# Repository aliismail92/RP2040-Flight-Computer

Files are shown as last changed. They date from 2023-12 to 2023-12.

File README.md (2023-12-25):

# RP2040-Flight-Computer
This is a custom drone flight computer based on RP2040. The KiCad files are available in addition to the production files to be produced by JLC PCB.

The Flight computer has the following sensors:
  - MPU 6050 Inertia sensor
  - HMC5883L digital compass sensor
  - BMP280 pressure sensor

Other specified connectors that can be added:
  - SD-card connector at the bottom of the board
  - Two uart connectors for the Radio controller (tagged IBUS) and another for GPS (tagged GPS)
  - Broken GPIOs for NRF24L01 with proper pin locations

Additionally, the two I2C ports connected to the MPU6050 and BMP280 have the pins exposed for debugging purposes.

The board was produced and assembled by JLCPCB and working.

RP2040-Brain-v2 0

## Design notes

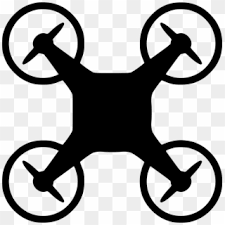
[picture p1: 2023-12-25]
images.png

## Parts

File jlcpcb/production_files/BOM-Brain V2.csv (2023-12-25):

Comment | Designator | Footprint | LCSC
1K | R2,R4 | R_0402_1005Metric | C11702
USB_B_Micro | J1 | USB_Micro-B_Molex-105017-0001 | C136000
10nF | C18 | C_0402_1005Metric | C15195
100nF | C10,C11,C12,C13,C14,C15,C16,C20,C21,C22,C23,C26,C28,C29,C3,C4,C6 | C_0402_1005Metric | C1525
30pF | C1,C2 | C_0402_1005Metric | C1562
2.2nF | C24 | C_0603_1608Metric | C1604
220nf | C30 | C_0402_1005Metric | C16772
4.7uF | C33,C7 | C_0603_1608Metric | C19666
10u | C25 | C_0603_1608Metric | C19702
RP2040 | U6 | QFN-56-1EP_7x7mm_P0.4mm_EP4x4mm_ThermalVias | C2040
1k | R18,R5 | R_0603_1608Metric | C21190
LED | D2,D3 | LED_0603_1608Metric | C2290
MPU-6050 | U4 | InvenSense_QFN-24_4x4mm_P0.5mm_NoMask | C24112
27 | R10,R9 | R_0603_1608Metric | C25190
10K | R1,R11,R12,R13,R14,R15,R16,R17,R19,R3,R6,R7 | R_0402_1005Metric | C25744
2.2K | R8 | R_0402_1005Metric | C25879
D_Schottky | D1 | D_SMA | C2909963
1u | C17,C19,C27 | C_0402_1005Metric_Pad0.74x0.62mm_HandSolder | C52923
22uF | C31,C5,C8,C9 | C_0603_1608Metric | C59461
AMS1117-3.3 | U2 | SOT-223-3_TabPin2 | C6186
BMP280 | U5 | Bosch_LGA-8_2x2.5mm_P0.65mm_ClockwisePinNumbering | C83291
Crystal_GND24 | Y1 | Crystal_SMD_3225-4Pin_3.2x2.5mm | C9002
W25Q128JVS | U1 | SOIC-8_5.23x5.23mm_P1.27mm | C97521

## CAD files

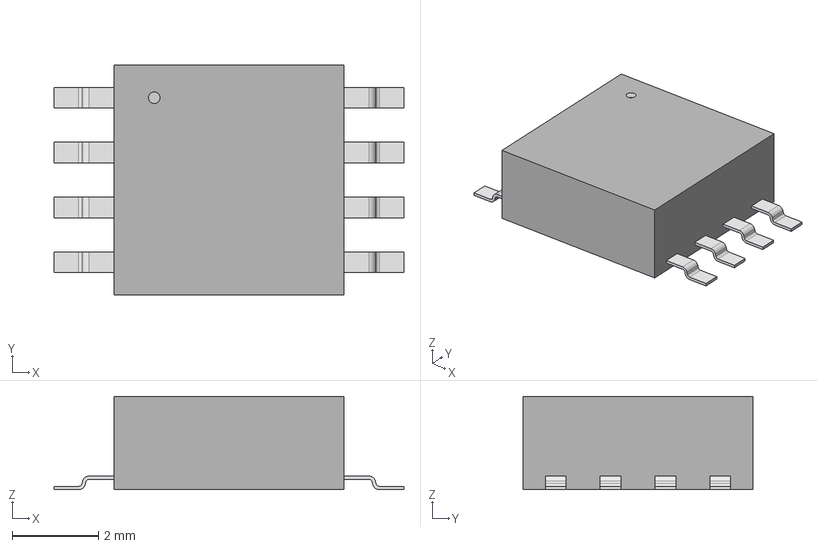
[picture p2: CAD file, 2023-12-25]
00-External Components/W25Q128_3D/SOIC_128JVSIM_WIN.step
8.10 x 5.33 x 2.16 mm

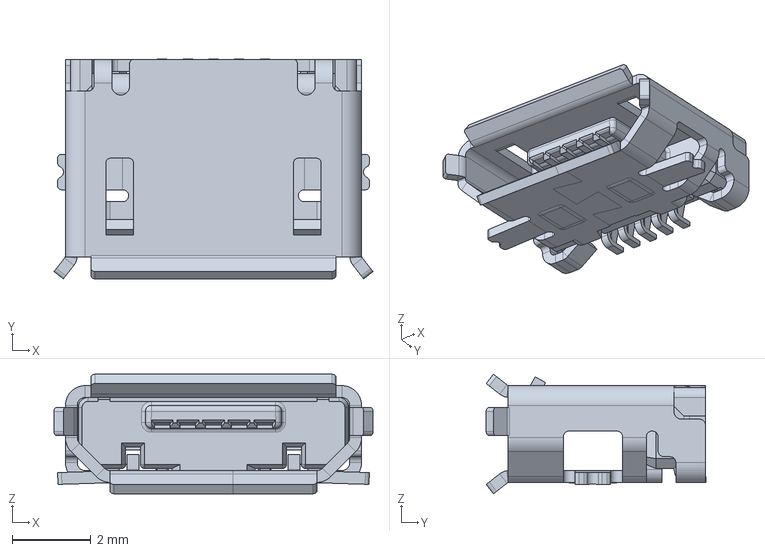
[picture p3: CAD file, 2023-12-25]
00-External Components/10104110-0001LF--3DModel-STEP-533217.STEP
8.08 x 5.56 x 3.03 mm

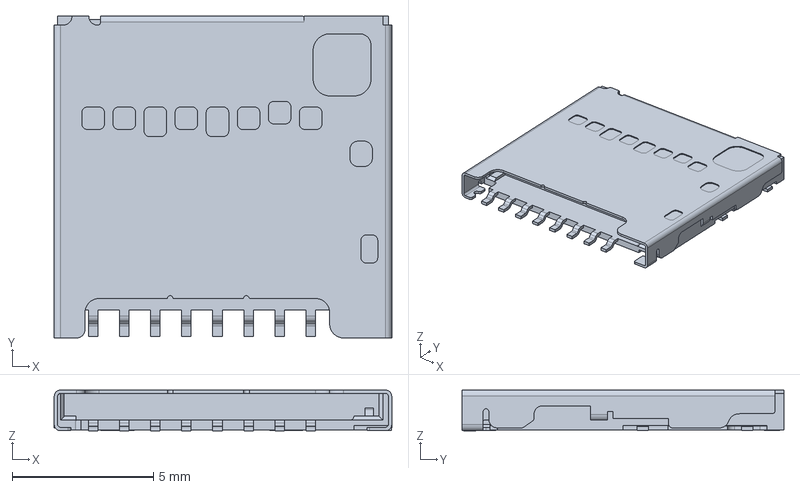
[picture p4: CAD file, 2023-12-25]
00-External Components/Molex 104031_SD_3D/1040310811.stp
11.9 x 11.4 x 1.45 mm

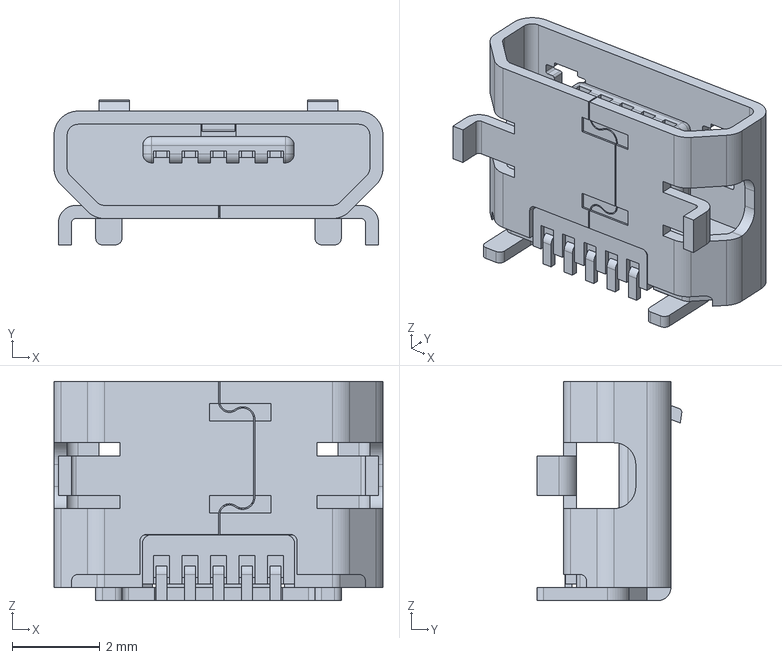
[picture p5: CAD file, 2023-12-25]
00-External Components/Molex 1050171_3D/1050171001.stp
7.50 x 3.30 x 5.00 mm

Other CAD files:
EdgeCut.dwg

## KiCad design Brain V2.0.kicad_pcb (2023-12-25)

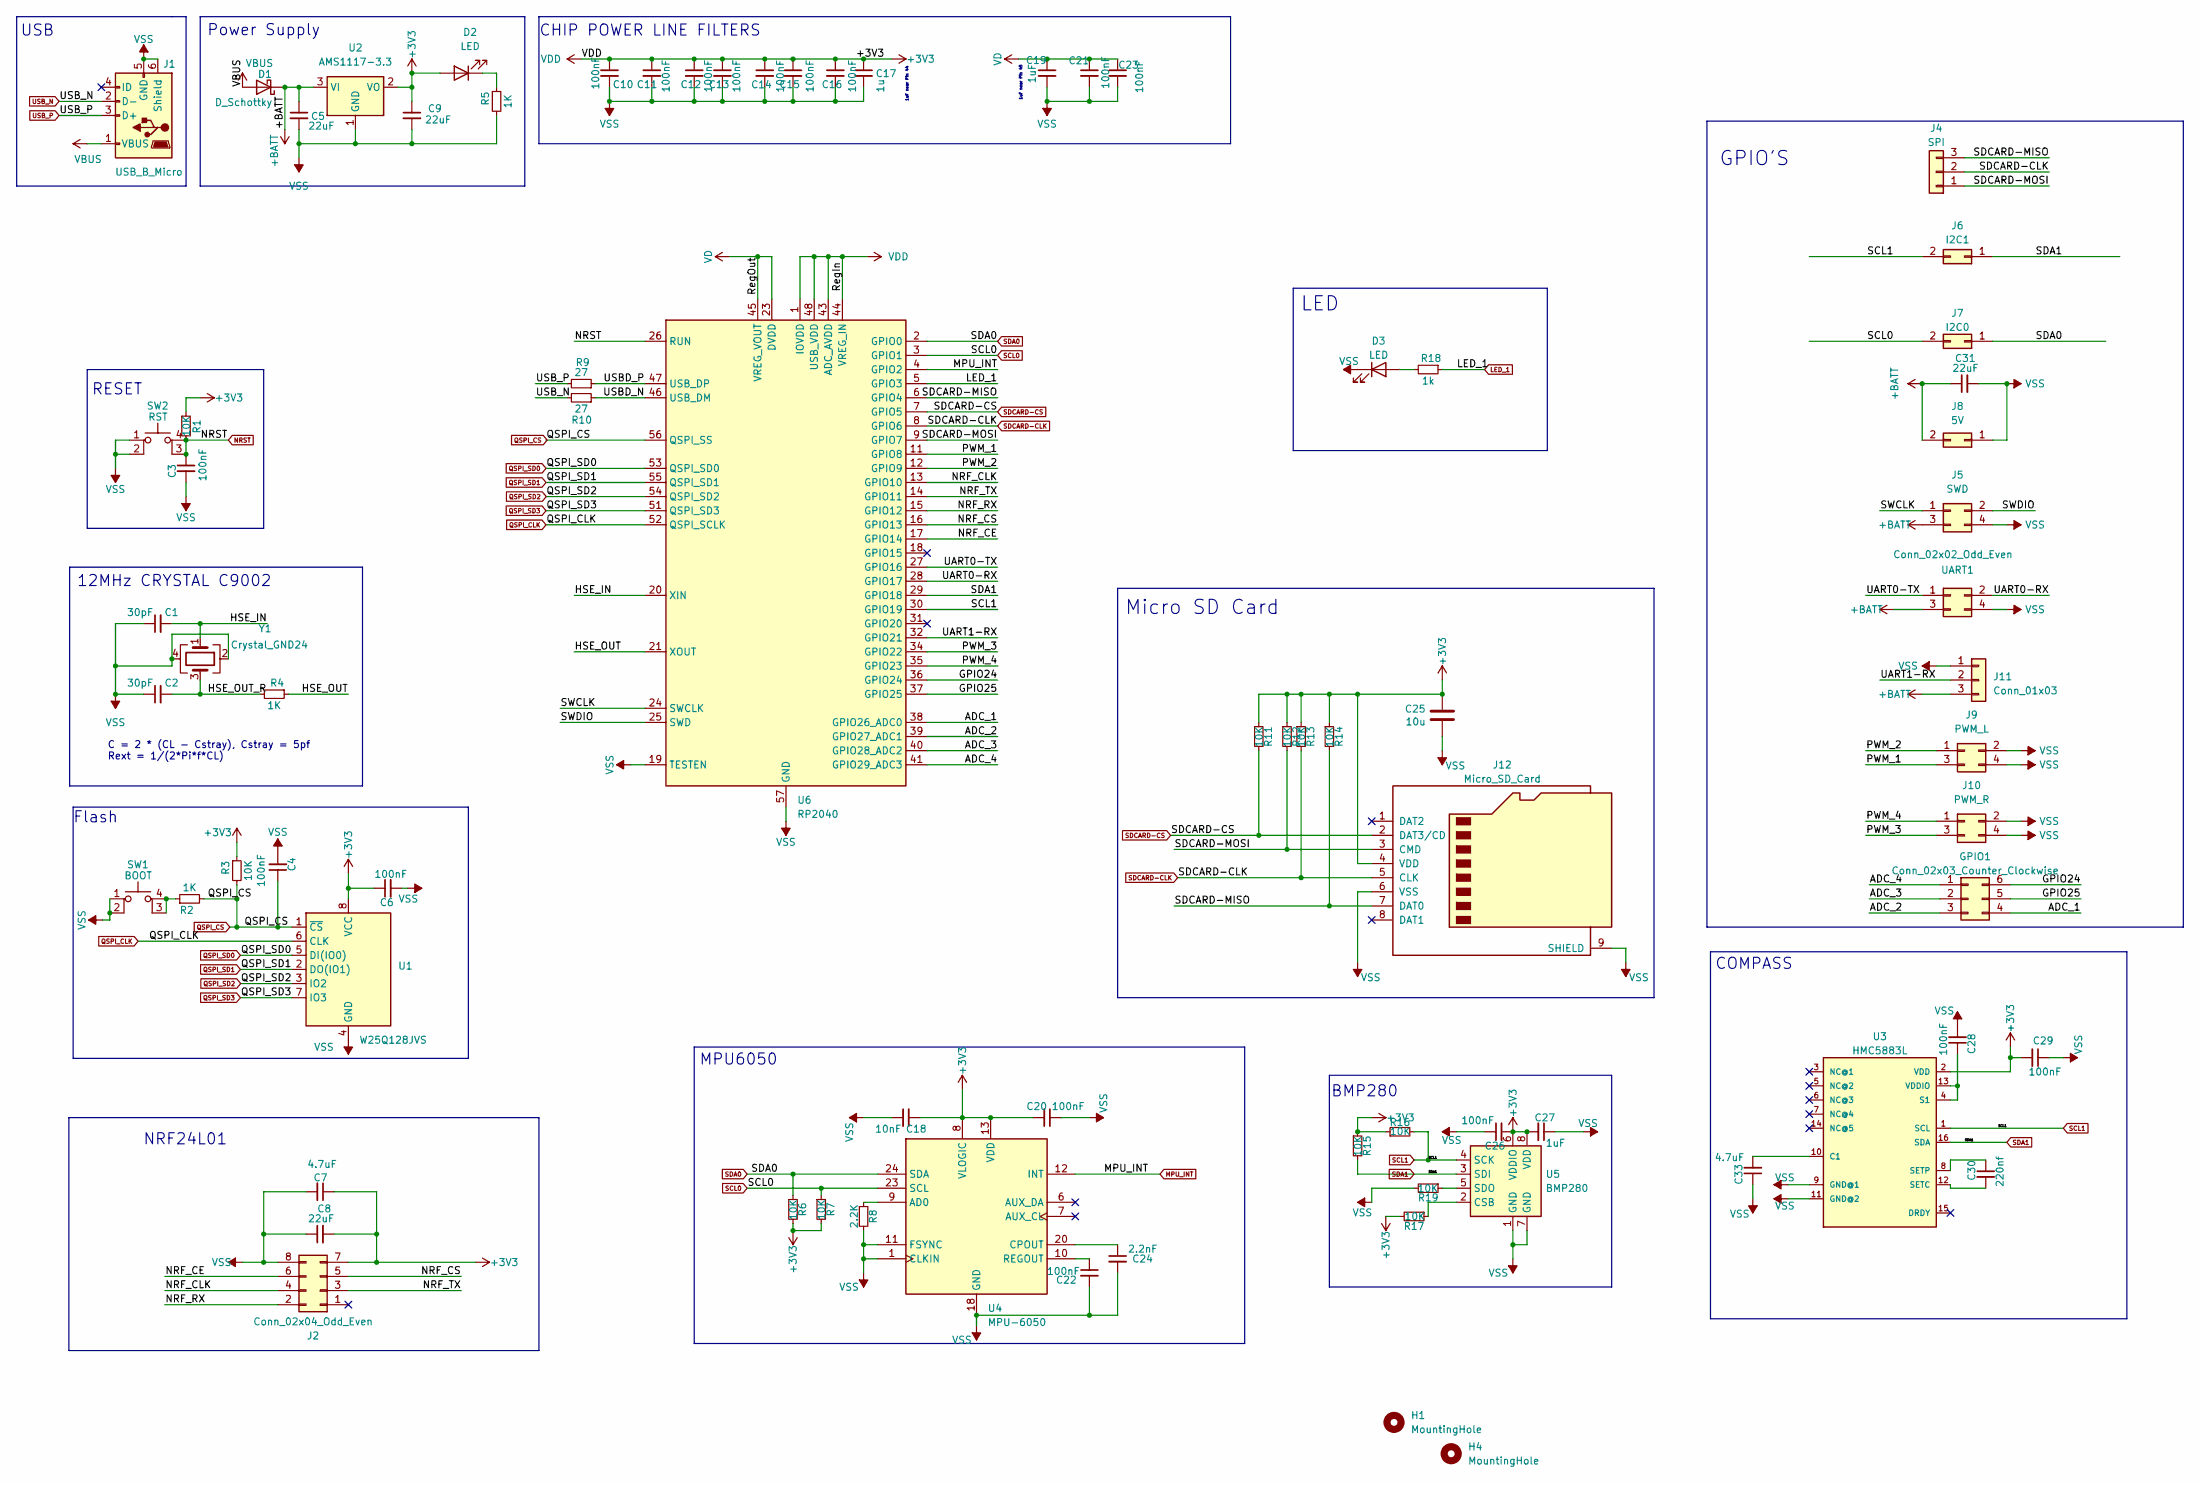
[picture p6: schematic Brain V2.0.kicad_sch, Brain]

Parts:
C1, C2: 30pF; C_0402_1005Metric
C3, C4, C6, C10, C11, C12, C13, C14, C15, C16, C20, C21, C22, C23, C26, C28, C29: 100nF; C_0402_1005Metric
C5, C8, C9, C31: 22uF; C_0603_1608Metric
C7, C33: 4.7uF; C_0603_1608Metric
C17: 1u; C_0402_1005Metric_Pad0.74x0.62mm_HandSolder
C18: 10nF; C_0402_1005Metric
C19: 1uF; C_0402_1005Metric_Pad0.74x0.62mm_HandSolder
C24: 2.2nF; C_0603_1608Metric
C25: 10u; C_0603_1608Metric
C27: 1uF; C_0402_1005Metric
C30: 220nf; C_0402_1005Metric
D1: D_Schottky; D_SMA
D2, D3: LED; LED_0603_1608Metric
GPIO1: Conn_02x03_Counter_Clockwise; PinHeader_2x03_P2.54mm_Vertical
H1, H4: MountingHole; MountingHole_4.3mm_M4
J1: USB_B_Micro; USB_Micro-B_Molex-105017-0001
J2: Conn_02x04_Odd_Even; PinHeader_2x04_P2.54mm_Vertical
J4: SPI; PinHeader_1x03_P2.54mm_Vertical
J5: SWD; PinHeader_2x02_P2.54mm_Vertical
J6: I2C1; PinHeader_2x01_P2.54mm_Vertical
J7: I2C0; PinHeader_2x01_P2.54mm_Vertical
J8: 5V; PinHeader_2x01_P2.54mm_Vertical
J9: PWM_L; PinHeader_2x02_P2.54mm_Vertical
J10: PWM_R; PinHeader_2x02_P2.54mm_Vertical
J11: Conn_01x03; JST_XH_B3B-XH-AM_1x03_P2.50mm_Vertical
J12: Micro_SD_Card; microSD_HC_Molex_104031-0811
R1, R3, R6, R7, R11, R12, R13, R14, R15, R16, R17, R19: 10K; R_0402_1005Metric
R2, R4: 1K; R_0402_1005Metric
R5: 1K; R_0603_1608Metric
R8: 2.2K; R_0402_1005Metric
R9, R10: 27; R_0603_1608Metric
R18: 1k; R_0603_1608Metric
SW1: BOOT; Button-01
SW2: RST; Button-01
U1: W25Q128JVS; SOIC-8_5.23x5.23mm_P1.27mm
U2: AMS1117-3.3; SOT-223-3_TabPin2
U3: HMC5883L; LPCC-16
U4: MPU-6050; InvenSense_QFN-24_4x4mm_P0.5mm_NoMask
U5: BMP280; Bosch_LGA-8_2x2.5mm_P0.65mm_ClockwisePinNumbering
U6: RP2040; QFN-56-1EP_7x7mm_P0.4mm_EP4x4mm_ThermalVias
UART1: Conn_02x02_Odd_Even; JST_XH_B4B-XH-A_1x04_P2.50mm_Vertical
Y1: Crystal_GND24; Crystal_SMD_3225-4Pin_3.2x2.5mm

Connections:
+3V3: C6.1, C7.1, C8.2, C9.1, C10.1, C11.1, C12.1, C13.1, C14.1, C15.1, C16.1, C17.1, C18.2, C20.2, C25.1, C26.2, C27.2, C29.2, D2.2 (A), J2.7, J12.4 (VDD), R1.1, R3.1, R6.2, R7.2, R11.1, R12.1, R13.1, R14.1, R15.1, R16.1, R17.2, U1.8 (VCC), U2.2 (VO), U3.2 (VDD), U4.8 (VLOGIC), U4.13 (VDD), U5.6 (VDDIO), U5.8 (VDD), U6.1 (IOVDD), U6.10 (IOVDD), U6.22 (IOVDD), U6.33 (IOVDD), U6.42 (IOVDD), U6.43 (ADC_AVDD), U6.44 (VREG_IN), U6.48 (USB_VDD), U6.49 (IOVDD)
+BATT: C5.1, C31.1, D1.1 (K), J5.3, J8.2, J11.3, U2.3 (VI), UART1.3
/ADC_1: GPIO1.4, U6.38 (GPIO26_ADC0)
/ADC_2: GPIO1.3, U6.39 (GPIO27_ADC1)
/ADC_3: GPIO1.2, U6.40 (GPIO28_ADC2)
/ADC_4: GPIO1.1, U6.41 (GPIO29_ADC3)
/GPIO24: GPIO1.6, U6.36 (GPIO24)
/GPIO25: GPIO1.5, U6.37 (GPIO25)
/HSE_IN: C1.2, U6.20 (XIN), Y1.1
/HSE_OUT: R4.1, U6.21 (XOUT)
/HSE_OUT_R: C2.2, R4.2, Y1.3
/NRF_CE: J2.6, U6.17 (GPIO14)
/NRF_CLK: J2.4, U6.13 (GPIO10)
/NRF_CS: J2.5, U6.16 (GPIO13)
/NRF_RX: J2.2, U6.15 (GPIO12)
/NRF_TX: J2.3, U6.14 (GPIO11)
/PWM_1: J9.3, U6.11 (GPIO8)
/PWM_2: J9.1, U6.12 (GPIO9)
/PWM_3: J10.3, U6.34 (GPIO22)
/PWM_4: J10.1, U6.35 (GPIO23)
/SDCARD-MISO: J4.3, J12.7 (DAT0), R14.2, U6.6 (GPIO4)
/SDCARD-MOSI: J4.1, J12.3 (CMD), R12.2, U6.9 (GPIO7)
/SWCLK: J5.1, U6.24 (SWCLK)
/SWDIO: J5.2, U6.25 (SWD)
/UART0-RX: U6.28 (GPIO17), UART1.2
/UART0-TX: U6.27 (GPIO16), UART1.1
/UART1-RX: J11.2, U6.32 (GPIO21)
/USBD_N: R10.1, U6.46 (USB_DM)
/USBD_P: R9.1, U6.47 (USB_DP)
LED_1: R18.1, U6.5 (GPIO3)
MPU_INT: U4.12 (INT), U6.4 (GPIO2)
NRST: C3.1, R1.2, SW2.3 (K), SW2.4 (A), U6.26 (RUN)
unnamed: D2.1 (K), R5.1
unnamed: D3.2 (A), R18.2
unnamed: R2.1, SW1.3 (K), SW1.4 (A)
unnamed: C33.2, U3.10 (C1)
unnamed: C28.1, U3.4 (S1), U3.13 (VDDIO)
unnamed: C30.2, U3.12 (SETC)
unnamed: C30.1, U3.8 (SETP)
unnamed: R8.1, U4.9 (AD0)
unnamed: C24.1, U4.20 (CPOUT)
unnamed: C22.1, U4.10 (REGOUT)
unnamed: R17.1, U5.2 (CSB)
unnamed: R19.1, U5.5 (SDO)
QSPI_CLK: U1.6 (CLK), U6.52 (QSPI_SCLK)
QSPI_CS: C4.1, R2.2, R3.2, U1.1 (~CS), U6.56 (QSPI_SS)
QSPI_SD0: U1.5 (DI(IO0)), U6.53 (QSPI_SD0)
QSPI_SD1: U1.2 (DO(IO1)), U6.55 (QSPI_SD1)
QSPI_SD2: U1.3 (IO2), U6.54 (QSPI_SD2)
QSPI_SD3: U1.7 (IO3), U6.51 (QSPI_SD3)
SCL0: J7.2, R7.1, U4.23 (SCL), U6.3 (GPIO1)
SCL1: J6.2, R16.2, U3.1 (SCL), U5.4 (SCK), U6.30 (GPIO19)
SDA0: J7.1, R6.1, U4.24 (SDA), U6.2 (GPIO0)
SDA1: J6.1, R15.2, U3.16 (SDA), U5.3 (SDI), U6.29 (GPIO18)
SDCARD-CLK: J4.2, J12.5 (CLK), R13.2, U6.8 (GPIO6)
SDCARD-CS: J12.2 (DAT3/CD), R11.2, U6.7 (GPIO5)
USB_N: J1.2 (D-), R10.2
USB_P: J1.3 (D+), R9.2
VBUS: D1.2 (A), J1.1 (VBUS)
VD: C19.1, C21.1, C23.1, U6.23 (DVDD), U6.45 (VREG_VOUT), U6.50 (DVDD)
VSS: C1.1, C2.1, C3.2, C4.2, C5.2, C6.2, C7.2, C8.1, C9.2, C10.2, C11.2, C12.2, C13.2, C14.2, C15.2, C16.2, C17.2, C18.1, C19.2, C20.1, C21.2, C22.2, C23.2, C24.2, C25.2, C26.1, C27.1, C28.2, C29.1, C31.2, C33.1, D3.1 (K), J1.5 (GND), J1.6 (Shield), J2.8, J5.4, J8.1, J9.2, J9.4, J10.2, J10.4, J11.1, J12.6 (VSS), J12.9 (SHIELD), R5.2, R8.2, R19.2, SW1.1, SW1.2, SW2.1, SW2.2, U1.4 (GND), U2.1 (GND), U3.9 (GND@1), U3.11 (GND@2), U4.1 (CLKIN), U4.11 (FSYNC), U4.18 (GND), U5.1 (GND), U5.7 (GND), U6.19 (TESTEN), U6.57 (GND), UART1.4, Y1.2, Y1.4

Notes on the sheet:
RESET
GPIO'S
1uF near Pin 45
MPU6050
CHIP POWER LINE FILTERS
BMP280
12MHz CRYSTAL C9002
LED
Micro SD Card
COMPASS
NRF24L01
Flash
C = 2 * (CL - Cstray), Cstray = 5pf Rext = 1/(2*Pi*f*CL)
Power Supply
USB
1uF near Pin 44

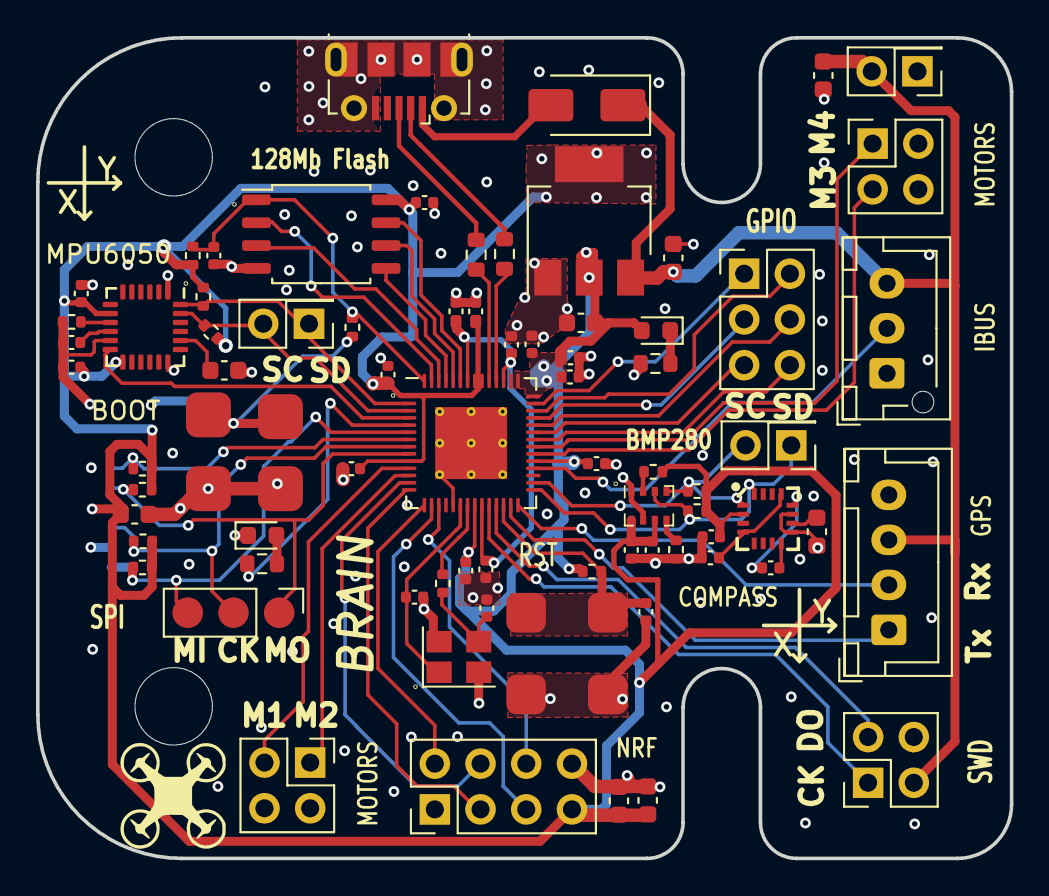
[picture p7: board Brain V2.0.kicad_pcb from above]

Board: 4 copper layers, 54.1 x 45.6 mm, 78 parts (1 on the bottom side), 61 nets.
